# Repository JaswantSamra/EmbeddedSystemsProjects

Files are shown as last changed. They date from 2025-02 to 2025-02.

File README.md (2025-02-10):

# EmbeddedSystemsProjects
 General Repository of my Embedded Systems adventures

## Garage Opener
Motivation: Currently working retail with mainly late night shifts and I wanted a way to open my garage door without having to wake up parents every singly time. <br/>
Project Goal: Be able to open my garage door without a dedicated remote.

### Project Resources:
1 x Adafruit QT Py ESP32-S3 (4MB Flash, 512KB SRAM, 2MB PSRAM) - This was definitely a much higher spec than what was needed. <br/>
1 x Inland 8 Channel 5v Relay - Way too many channels (future expandability I guess) but was also the only one available in-person. <br/>
3 x M to F Dupont jumpers (I cut off the male side and soldered the cut wire to the pins I needed.) <br/>
1 x 3D printed case (STL attached.) <br/>

### Initial Attempts: 
1) Using ESP32 as the remote with a spare nRF24L01.
2) Having ESP32 host a site internally on my WiFi.
3) Using Blynk Services with my ESP32 and a 5V relay.

### Why 1 & 2 didn't work:
1) nRF24L01 works at 2.4 ghz when most garage remotes work between the range of 300 - 433.92 mhz. Garage Remotes also have oscillators/ crystals in them that are essential to creating a rolling code. Even if I could capture one of the rolling codes, I would have to constantly reprogram the remote as the codes would change after a set period of time.
2) The HTML code was written in one line and I did not want to do that to myself or anyone who tries this project out. This could've worked but for my sanity, I did not go this route. Also, family has a mixture of iOS and Android devices and I wanted to make sure that no matter what, it looked the same for both operating systems. I would also have to come home tired after work, connect to the WiFi, then go to the websites internal IP address and then finally press the button. I want something a bit easier to access.

### Why Blynk?
It was the first free service I saw that allowed me a good number of features: up to 10 devices, 10 templates, and 30000 monthly messages. It also has really good documentation and templates that help you get started. 

### Case Design: 
* [Mykorhiza's 8 Channel 5V Relay](https://www.thingiverse.com/thing:3212197)
* [Adafruit QT Py ESP32-S3 Model](https://github.com/adafruit/Adafruit_CAD_Parts/blob/main/5426%20QT%20Py%20ESP32-S3/5426%20QT%20Py%20ESP32-S3.stl)

Using these two models & TinkerCAD, I was able to combine them both with my very novice 3D modeling skills and make an area that I was happy with to store the esp32-S3. The area created is slightly ugly with its pointy corners but it works. There is also 3 total holes in the area for air flow, access for the jumper cables to pass through, and the USB-C port on the front of the ESP32. 

### Pros:
* I got to make one of my first 3D models
* Very cool to see how well everything fit together in the end.
* DIY Project for a big Quality of Life improvement.
### Cons:
* The area created specifically for the ESP32 board is way too tall. I would trim it down by 2mm-ish.
* The main sketchy part was having to trim down the pcb of the 5v relay but I made sure there were no traces near where I cut the board. I covered the cut edges with hot glue to both insulate the motherboard's now exposed layers but to also make sure the relay stuck to the case. If I did this again, I would increase the length of the case by about 1-3 mm so I didn't have to grind/cut the pcb. It was nervewracking cutting the pcb with flush cutters.

Wiring Diagrams: 
Please see the images in the folder.

Text Diagram: 

ESP32 S3 <br/>
Used Pins: <br/>
```
5V  ------------------------   
GND ------------------     |   
A0 -------------     |     |   
               |     |     |   
5V Relay       |     |     |   
IN_0 -----------     |     |   
GND ------------------     |   
VCC ------------------------   
```
5V Relay to Garage Door Button <br/>

IN_0 has: <br/>
NO <br/>
COM <br/>
NC <br/>
denoted as such on the board: <br/>
NO --------\ <br/> 
<br/>
COM -------\ <br/>
NC --------/ <br/>

Garage Door Button has 4 connections denoted by the color of the wire: White, Black, Green, Yellow. <br/>

Using a multimeter on Continuity ( V with a solid line ) mode: <br/>

Continuity exists between:
* White and Black
* White and Green

Continuity is not between:
* Black and Green
* Black and Yellow

Shorting the White and Black wire using an insulated solid core wire resulted in the door opening leading to the following assumptions: <br/>
White was COM  <br/>
Green was NC   <br/>
Black was NO   <br/>
Yellow is the Sensor input

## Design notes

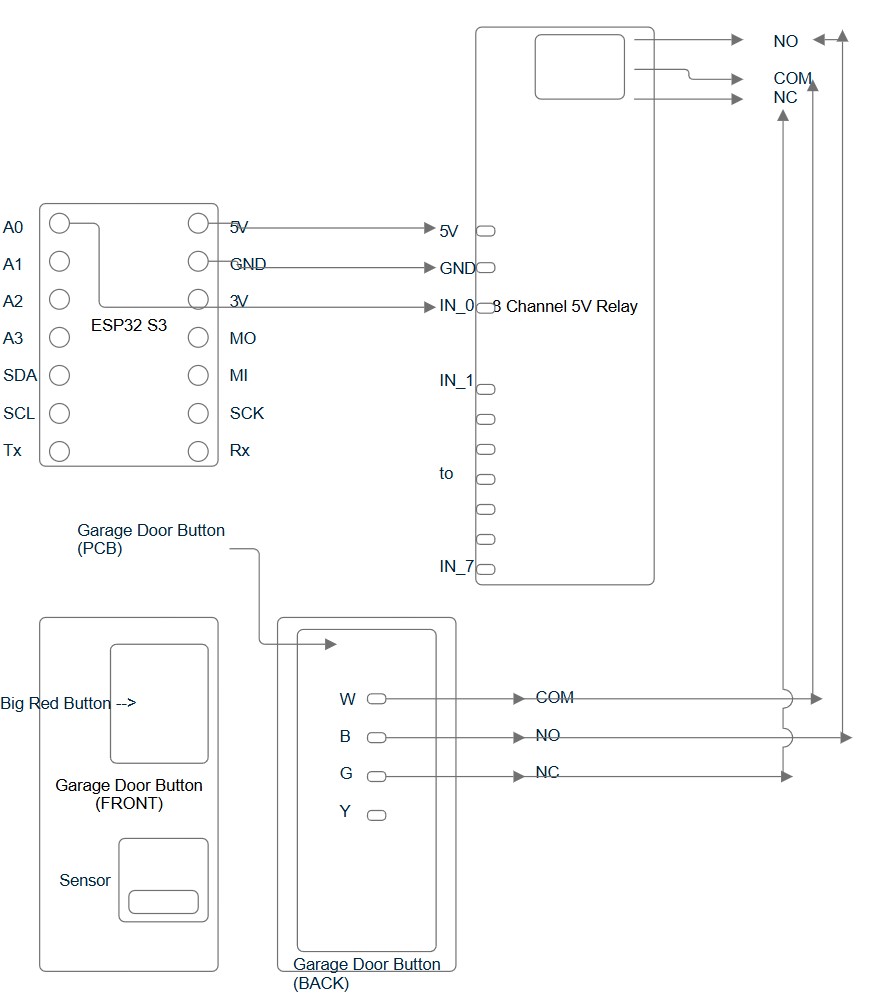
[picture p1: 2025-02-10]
GarageOpener/GarageOpener.jpg

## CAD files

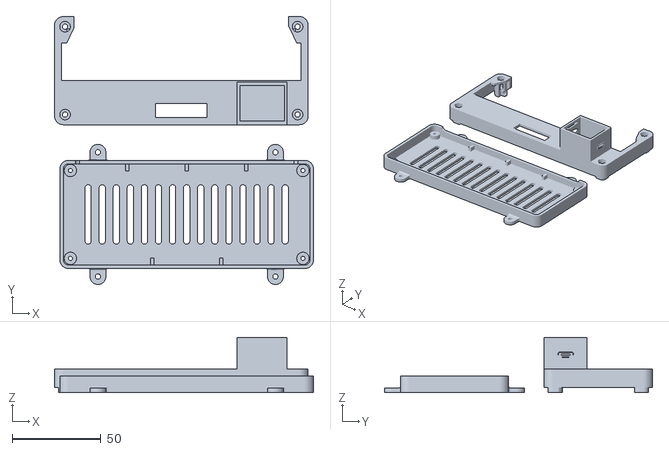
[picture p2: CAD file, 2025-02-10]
GarageOpener/8Channel5VRelay+ESP32Case.stl
146.0 x 151.0 x 31.0

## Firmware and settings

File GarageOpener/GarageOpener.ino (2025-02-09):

#define BLYNK_TEMPLATE_ID "BLYNK_TEMPLATE_ID"         //just my template ID from the Blynk Service
#define BLYNK_TEMPLATE_NAME "ESP32 S3"                //Adafruit QT Py ESP32-S3 (with the onboard storage and RAM) is the board I used.
#define BLYNK_AUTH_TOKEN "BLYNK_AUTH_KEY"

#define BLYNK_PRINT Serial                            //Redefines the Blynk 'status prints' to print out to a Serial monitor port of your choice


#include <WiFi.h>
#include <WiFiClient.h>
#include <BlynkSimpleEsp32.h>

char ssid[] = "WiFi_NAME";
char pass[] = "WiFi_PASSWORD";

#define RELAY_PIN A0

BLYNK_WRITE(V0) {                                     //Using Virtual Pin 0 to capture and relay signal
  if (param.asInt() == 1) {                           //param.asInt() used to grab input from V0
    digitalWrite(RELAY_PIN, HIGH);                    //Activate relay
    //Serial.println("🔴 Relay Activated (Garage Door Opening)"); //Debug through Console
    delay(500);                                       //hold for 0.5 sec
    digitalWrite(RELAY_PIN, LOW);                     //Deactivate relay
    //Serial.println("⚪ Relay Deactivated (Garage Door Closed)"); //Debug through Console
  }
}

void setup() {
  Serial.begin(115200);                               //Setting BAUD rate to 115200

  //Serial.println("🚀 Starting Virtual Garage Door Controller...");

  pinMode(RELAY_PIN, OUTPUT);                         //Pin configuration, letting it be set as either Input or Output. For the purposes of this project, it is in Output mode.
  digitalWrite(RELAY_PIN, LOW);                       //Starts on LOW


  Blynk.begin(BLYNK_AUTH_TOKEN, ssid, pass);          //Starts talking with Blink Service through the passed-in parameters
}

void loop() {
  Blynk.run();                                        //Runs the Blink Service
}

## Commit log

2025-02-09 Create GarageOpener.ino
    Working commit with Debug Messages. This is it until I want to add in sensor inputs.
2025-02-10 Modified Case to Fit ESP32 + Wiring Diagram
    Source Work:
    https://www.thingiverse.com/thing:3212197
    https://github.com/adafruit/Adafruit_CAD_Parts/blob/main/5426%20QT%20Py%20ESP32-S3/5426%20QT%20Py%20ESP32-S3.stl
    Modified into one file to add a mount for an ESP32 onto the case from Thingiverse.
    Wiring Diagram is simplistic but captures all hardwire connections for running this setup in parallel.
    [8Channel5VRelay+ESP32Case.stl]
